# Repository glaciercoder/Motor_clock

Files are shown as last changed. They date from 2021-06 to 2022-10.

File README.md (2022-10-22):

# Motor_clock

## Day 1:

看到了链接觉得很好玩，想自己搞一个。

首先考虑到静音的需求，企图使用小步进，配合TMC202x控制芯片来用。

感谢 *小山嘉* 提供步进电机链接，使用拆机小型步进，成本很低。

发现问题在于TMC202x成本过高。

考虑到每个电机只需要两个状态，打算使用双稳态电磁阀 

发现一个视频：

[Mechnical Design](httNs://www.youtube.com/watch?v=ukRGbEUAVtM&feature=youtu.be)

打算搞这个曲线就可以用最多6个电机完成控制。

## Day 2:

和 *李金时* 一起研究机械结构，发现一些问题

1. 如果将连杆固结在数字轴中心，，数字翻动时会导致连杆的上下运动，所以使用凸轮结构。
2. 发现上述视频里的方形数字有点儿丑，想采用菱形和梯形数字，但是菱形和梯形数字在转动时出现干涉的现象，所以对干涉的问题进行研究。

### 参数初步规定：

连杆内拉3mm从隐藏变为显示，杆直径2mm，凸轮壁厚1mm

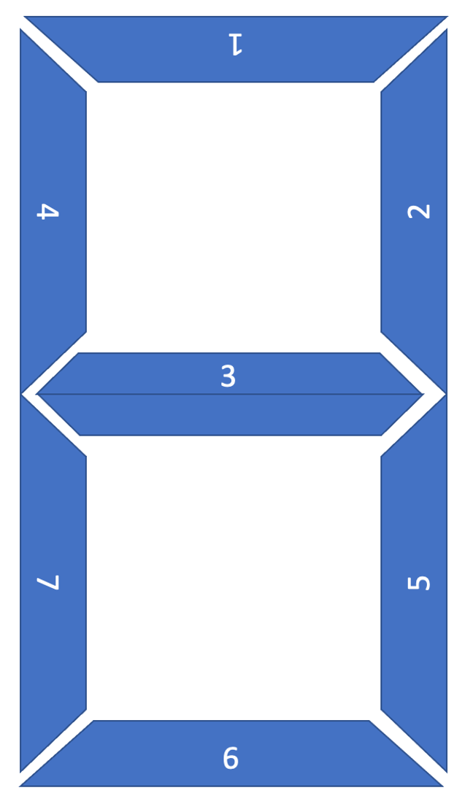
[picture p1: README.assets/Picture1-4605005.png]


### 凸轮设计：

记为放下状态(不显示)，为拉入状态（显示）

每$36^{\circ}$ 为一个变化时段，如果在该时段与下一时段交界处发生状态转变，则该时段最后$\Delta \theta$与下一时段$\Delta \theta$用于状态转变,对秒，$\Delta \theta = 10^{\circ}$;对分钟和小时,$\Delta \theta = 20^{\circ}$

| 编号/时序 |  1 | 2 | 3 | 4 | 5 | 6 | 7 | 8 | 9 | 0 |
| :---: | :--: | ---- | ---- | ---- | ---- | ---- | ---- | ---- | ---- | ---- |
| 1 |  N | P | P | N | P | P | P | P | P | P |
| 2 |  P | P | P | P | N | N | P | P | P | P |
| 3 |  N | P | P | P | P | P | N | P | P | N |
| 4 |  N | N | N | P | P | P | N | P | P | P |
| 5 |  P | N | P | P | P | P | P | P | P | P |
| 6 |  N | P | P | N | P | P | N | P | P | P |
| 7 |  N | P | N | N | N | P | N | P | N | P |

利用上述表格进行绘图，思考一番决定使用Matlab多项式拟合极坐标方程，$10^{\circ}$给一个点

发现完全没有必要，直接拿sw做，过渡处使用两段切线弧过渡

在一番苦战之后，终于把凸轮搞定了，下面将基于该尺寸完善连杆机构

## Day 3:

开始着手设计PCB，打算先拿一个板子，把配置都配好，在最终控制板上不再使用引脚配置TMC2208，

可以使用的其他电机驱动（A4998 TB6612FNG）

### PCB Design

考虑到电机供电问题，考虑使用电池供电,可通过外接电源切换

考虑到凸轮转动方向不变，可以将DIR全部共起来，同时考虑到秒针，分针时针凸轮转动频率相同，使用6个PWM引脚就可以，用PCA9685 I2C模拟PWM

时钟使用DS3231

## Day 4:

 意识到电机数量太多，功率较高，需要考虑怎么画转换电路，感谢 *高一川 梁迪轩* 的帮助

发现PCA9685 I2C模拟PWM的问题：输出PWM的频率都是相同的，这无法用于步进电机控制，所以用PCA来处理时钟和分钟8路PWM，秒针单独用两路PWM

## Day 5

发现DC5525可以通过机械结构直接断开内部电路，不同担心转换电路了,但是考虑到一个问题是，如果电源不是从DC005拔掉而是从插线板拔掉就出问题？

## Day 6

先把电机调通搞一套初步能用的代码，再继续画板子。

TMC2208可以使用USART模式（高级设置），也可以是向A4988那样使用简单的PWM输入，打算使用后者。但是电机第一次没有成功起转。后来发现应该将PDN引脚拉低，同时EN与单片机GND连接。

电机转动不太正常，主要的可能是该步进电机的额定电流未知，没有设置的比较好，打算买好一点的电机，再进行调试。

#### 学习用热风枪焊接IC

锡量极其重要，不要放太多，不然引脚大概率粘接

风速不能太低，不然多余焊锡熔而不走，也容易造成粘接

## Day 7

把电机调好了，真坑爹啊，以后一定要看清文档，M1A，M1B接的是一个绕组

Arduino delayMicrosecond 是微秒！

和李金时看了第一版结构，余量不足，无法装配

发现使用PCA9685的问题：如果使用PCA9685内部时钟，漂移可能会非常严重，如果使用外部时钟，配置困难且难以保证I2C正常工作，最终决定将电机驱动直接挂在GPIO上

在kicad里修改完footprint需要开一个新的lib保存，不然可能无法生效

开始layout了

## Day 8

layout好了，有几个问题需要思考：电机开环如何复位

准备使用红外对管进行复位

对于接地问题的讨论[接地](http://blog.sina.com.cn/s/blog_6471e1bb0100mrjp.html)

## Day 9

打样测试

## Day 10

考虑代码构建，使用状态机

[参考](https://learn.adafruit.com/multi-tasking-the-arduino-part-1)

每个loop先判断状态，用flag标记每个电机状态，然后用在mills执行相应动作

对于不同位置的电机设置不同的interval实现转动速度的控制

需要设计不同的细分

[millis rollover](https://arduino.stackexchange.com/questions/12587/how-can-i-handle-the-millis-rollover/12588#12588)

考虑一种处理溢出的方法：手写高精度,但实际上

[This is not a problem](https://www.gammon.com.au/millis)

## Day11

处理归零问题，机械归零不太好，设计了一种对管的方案：

使用一个狭缝，对对管的发射进行限制，然后在转盘上设计狭窄突出，与狭缝配合，提高精度，但是考虑到读取精度可能不高，而且加工精度也达不到很高，遂放弃该方案

采用磁编码器，使用AS5600，考虑到淘宝没有能够适用电机尺寸的PCB，打算自己设计

打算使用角块的方式进行盒子的装配，这样可以使装配变得简单

AS5600 不能设I2C地址，无语子

貌似AS5600L可以，但是也没说怎么设？ 无语子

*高一川* 给出针对I2C无法修改地址的应对策略，使用TCA9548A，非常有价值

## Day 12

第一次设计的PCB到了，有一个元件没有贴，极其难受，先尝试烧录程序，并调试DS3231

第一版板子的问题：

LED_Pin不在PWM引脚，修改DIR

没贴全

USB画反了，USB有没有画反取决于引脚顺序，而不是外形

软件部分，buffer难以清空，想写一个依靠串口进行初始化的程序。

## Day 13

画AS5600pcb

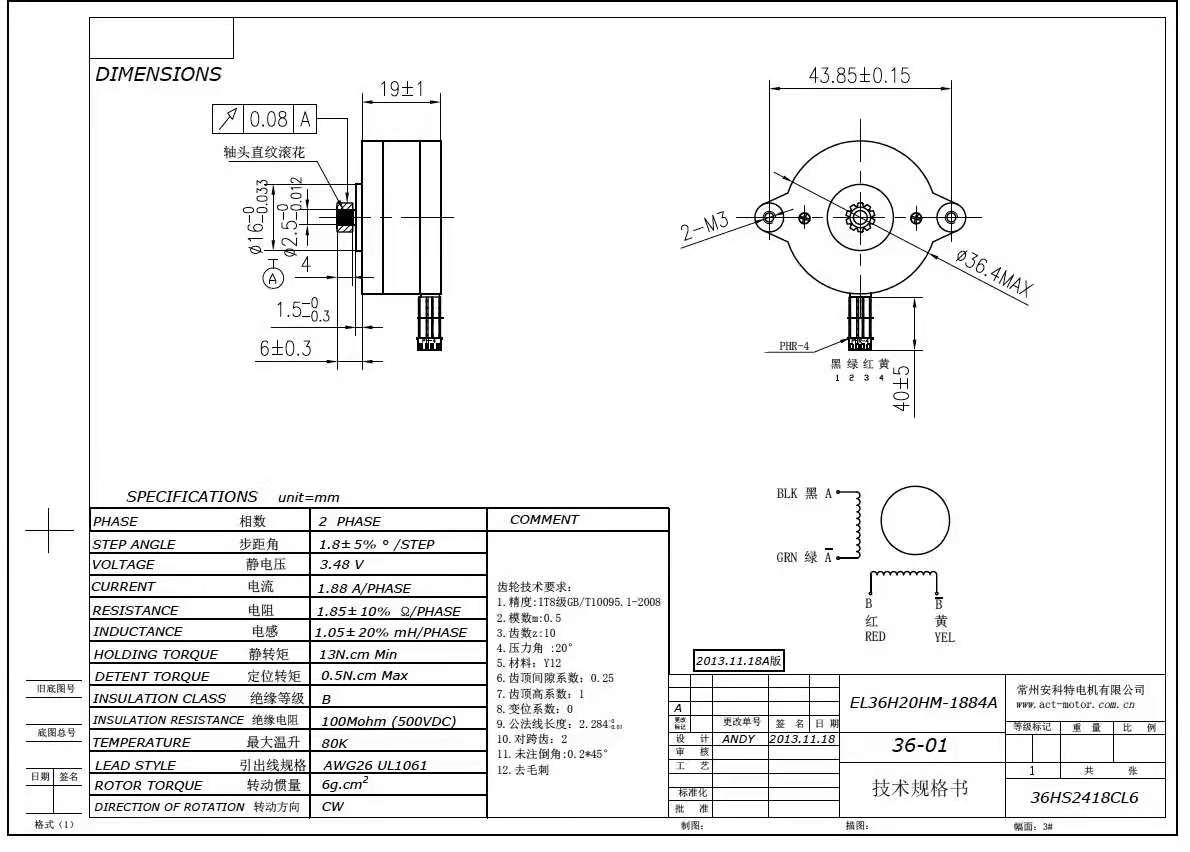
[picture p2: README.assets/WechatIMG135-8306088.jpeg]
WechatIMG135


修改第一版PCB，bug极多

1. ICSP接法：不是把一个的ICSP完全接到另一个的ICSP，targetRESET接法不一样！！！！！！需要接到10上
2. 不要在TX，RX上做LED，会让电压漂移
3. DTR必须接，不然不work，必须在DTR引脚到RESET之间串100nF电容，不然不work
4. CR3202 封装有问题

## Day14

调试第一版PCB，所用功能均正常

修改第一版PCB

1. 删去了DS3231的reset按钮，与MCU共RESET
2. PDN 直接接地
3. 加入了编码器接口
4. 加入蜂鸣器
5. 删去了无用的丝印
6. 修正了第一版的bug

机械装配遇到困难，采用数字板和连杆使用金属加工，其他部分3D打印的加工方式

## Day 15

讨论新的机械加工方案，打算使用齿轮传动，用固定座上的齿条驱动零件转动，但是加工仍然存在困难，考虑将元件放大两倍。

讨论盒子的设计方案

## Day 16

打印第二版零件，框加工有点儿贵，打算买现成的

南方小厂小批零件加工比北方大厂便宜很多，铝合金可直接激光切

## Day 17

调试第二版电路板，装配第二版机械零件。

第二版电路板控制部分工作正常，电源模块有问题，插上DC口出现烧坏的迹象，同时插入USB开始冒烟。4.7uH 电感挂了.

可能原因：电感许可电流太小，这是有可能的，在带LED之后确实需要比较大的电流输入，但是问题是没有接LED也挂了。 

六个电机接好，有一个不转，检查多次后无果，*夏博文* 提供帮助，发现是焊接connector时灌入过多的锡，导致connector在正面短路，焊接时一定要注意不能灌锡，应该尽量在一侧形成焊点。

六个编码器有一个不工作，怀疑是芯片的问题，打算重新做芯片

第三版软硬件修改：

1. 取消DS3231 RESET，实现一次上电一直记时的效果，对应的，把软件改成开机读取现在的时间，然后机械对钟。
2. 设置串口中断，只在接受到特定信号的时候进行DS3231设置
3. 将DIR换到非PWM引脚
4. 重画Buzzer电路，GPIO直接推不动

修改机械，使用内螺纹圆柱

内螺纹圆柱销 内径4x12x M3 100

M3x10 200个

## Day 18 19

重新修改机械结构，积累如下经验
==3D打印尽量设计螺丝固定等机构,尽可能少设计拼插==

==尽可能不要设计内槽道等结构，容易因为支撑等原因造成较大的误差==

==3D打印出的孔需要过一遍钻来保证精度==

==可以把层状3维结构拆分成2维，便于加工==

==sw建模使用树状装配体结构，将配合放在文件夹中便于修改，不要野配合==

==可以在适当的位置打孔，从而节省外包3D打印成本==

和李金时一起修3D打印机，

## Day 20
和nlc一起改了板子，主要是修改了电感的封装，新的板子功能正常。 <br/>
机械机构方面,nlc对齿条进行了两次修改，第一次延长了齿条长度，但是发现这个修改并不能解决啮合的问题，因此尝试将齿条整体抬高0.3mm，但是出现了上面的齿轮和齿条卡住的情况，对此，解决方案是把齿轮的高度下调一些。

## Day 21

- 发现一个大bug，凸轮结构控制滑块，考虑到每一层轨道控制的滑块要顺延90度，对应的轨道应该也转90度。

## Day 22

- nlc对底座进行了加强，避免了因底座在受力的情况下发生弯曲进而导致滑齿。

- ylw同学为了降低摩擦力非法使用了WD40，特此通报批评。

- wbc同学在调试过程中烧坏TMC2208一枚，工程经验又++。

## Day 23

- 302的门开了，nlc与wbc组装了一个完整的数字，调试顺利，而且噪声比预想的小很多。TMC2209驱动板的扭矩还是足够的。
  
  (https://youtube.com/shorts/_J2np6-Vw0g?feature=share)
  
 - 依然存在的问题&解决方案

    - 齿轮偶尔存在打滑的现象，原因可能是铜柱松动。由于无法精确设计铜柱的孔径大小，决定在竖直方向开孔，用M3螺丝锁住铜柱

## Day 24

- 新打印了座子与滑块，存在如下问题：

  - 由于3D打印机打印竖直方向的孔误差很大，M3螺丝容易打滑，考虑的解决方案是减小孔径。
  
  - 由于之前钢柱没完全固定，所以没有发现滑块和齿轮啮合过于紧的问题，打算先打印出来组装看看电机扭矩够不够。如果电机扭矩不够就降低滑块高度。

### 资料整理

[机械结构设计](httNs://www.youtube.com/watch?v=ukRGbEUAVtM&feature=youtu.be)

[TMC2208驱动](https://wiki.fysetc.com)

[TMC 接线](https://blog.csdn.net/weixin_42740222/article/details/88637535)

[Arduino TMC2208 lib](https://www.arduino.cc/reference/en/libraries/tmc2208stepper/)

[PCA9685电路设计](https://wenku.baidu.com/view/826d0d257c1cfad6185fa75c.html)

[PCA Arduino](https://learn.adafruit.com/16-channel-pwm-servo-driver/hooking-it-up)

[转换电路](https://www.eet-china.com/mp/a33537.html)

[DC5525](https://ask.zol.com.cn/x/5491238.html)

[Pin Mapping](https://www.arduino.cc/en/Hacking/PinMapping168)

[ATmega 328P-AU](https://forum.arduino.cc/t/atmega328-au/550838)

[Adafruit](https://learn.adafruit.com)

[AS5600](https://ams.com/as5600#tab/description)

[AS5600L](https://ams.com/documents/20143/36005/AS5600L_DS000545_3-00.pdf/7ade6878-7a32-2294-b88d-479d50fab6de)

[TCA9548](https://learn.adafruit.com/adafruit-tca9548a-1-to-8-i2c-multiplexer-breakout/downloads)

[I2C上拉电阻](https://www.zlg.cn/ipc/article/detail/id/690.html)

### 开销

中性笔(x)

买电机驱动模块 6个(x)

Niextube

嘉里创元件费（x）

云汉芯城元件费(x)

板子（x）

转接头（x）

DS3231模块(第一次)

DS3231模块(第二次) 

3D打印（200）

TCA9548A 模块

TPS561208DDCR

AS560 芯片(第一次)(x)

AS5600 芯片(第二次)

TCA9548A 芯片（30）

立创商城元件(x)

LED板（x）

第二次机械加工（860）

金属动板 (150)

嘉立创邮寄元件：TPS561208DDCR，TCA9548A(x), CH340G(x), 

WS2812(3m)(x)

邮寄处理费(x)

老铁：

中午吃饭. 51.5 (x)

《网络是怎样连接的》 91.64(x)

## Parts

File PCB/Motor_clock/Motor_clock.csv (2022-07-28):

ID | 指示符 | 软件包 | 数量 | 名称 | 供应商和参考
1 | VR1 | SOT95P280X110-6N | 1 | TPS561208DDCR
2 | BT1 | TE_796136-1 | 1 | BT_3v3
3 | C1 | C_0603_1608Metric | 1 | 100pF
4 | C2,C4 | C_0603_1608Metric | 2 | 1uF
5 | C3,C6,C13,C11 | C_0603_1608Metric | 4 | 22pF
6 | C5 | C_0805_2012Metric | 1 | 4.7uF
7 | C7 | C_0805_2012Metric | 1 | 22u
8 | C8 | C_0603_1608Metric | 1 | 0.1uF
9 | C9 | C_0805_2012Metric | 1 | 47uF
10 | D1 | LED_0603_1608Metric | 1 | LED
11 | J1 | JST_XH_S3B-XH-A-1_1x03_P2.50mm_Horizontal | 1 | WS2812
12 | J3 | JST_PH_S2B-PH-K_1x02_P2.00mm_Horizontal | 1 | Battery_input
13 | J4 | PinHeader_2x03_P2.54mm_Vertical | 1 | ICSP
14 | J5,J7 | JST_PH_B4B-PH-K_1x04_P2.00mm_Vertical | 2 | M_H_1
15 | J6 | JST_PH_B4B-PH-K_1x04_P2.00mm_Vertical | 1 | M_S_1
16 | J8 | JST_PH_B4B-PH-K_1x04_P2.00mm_Vertical | 1 | M_S_2
17 | J9 | JST_PH_B4B-PH-K_1x04_P2.00mm_Vertical | 1 | M_M_1
18 | J10 | JST_PH_B4B-PH-K_1x04_P2.00mm_Vertical | 1 | M_M_2
19 | L1 | L_7.3x7.3_H4.5 | 1 | 4.7uH
20 | R1,R3,R4,R8,R9 | R_0603_1608Metric | 5 | 1k
21 | R2,R5 | R_0603_1608Metric | 2 | 4k7
22 | R7 | R_0603_1608Metric | 1 | 10k
23 | SW2 | SW_Push_1P1T_NO_6x6mm_H9.5mm | 1 | SW_Push
24 | U2 | TQFP-32_7x7mm_P0.8mm | 1 | ATmega328P-AU
25 | Y1 | Crystal_SMD_3225-4Pin_3.2x2.5mm | 1 | 16Mhz
26 | U3 | TMC2208 | 1 | M_H_1
27 | U4 | TMC2208 | 1 | M_S_1
28 | U5 | TMC2208 | 1 | M_H_2
29 | U6 | TMC2208 | 1 | M_S_2
30 | U7 | TMC2208 | 1 | M_M_1
31 | U8 | TMC2208 | 1 | M_M_2
32 | J2 | NINIGI_DC-005 | 1 | Barrel_Jack_Switch
33 | H2,H4,H3,H1 | MountingHole_3.2mm_M3 | 4 | MountingHole
34 | J12 | JST_PH_B4B-PH-K_1x04_P2.00mm_Vertical | 1 | Enc_M_2
35 | J13 | JST_PH_B4B-PH-K_1x04_P2.00mm_Vertical | 1 | Enc_H_2
36 | J14 | JST_PH_B4B-PH-K_1x04_P2.00mm_Vertical | 1 | Enc_S_2
37 | J15 | JST_PH_B4B-PH-K_1x04_P2.00mm_Vertical | 1 | Enc_S_1
38 | J16 | JST_PH_B4B-PH-K_1x04_P2.00mm_Vertical | 1 | Enc_M1
39 | J17 | JST_PH_B4B-PH-K_1x04_P2.00mm_Vertical | 1 | Enc_H_1
40 | U10 | TSSOP-24_4.4x7.8mm_P0.65mm | 1 | TCA9548APWR
41 | U1 | SOIC-16W_7.5x10.3mm_P1.27mm | 1 | DS3231M
42 | C10 | C_0603_1608Metric | 1 | 10uF
43 | C12,C14,C15 | C_0603_1608Metric | 3 | 100nF
44 | D2,D3 | D_SMA | 2 | 1N5819
45 | Y2 | Crystal_SMD_3225-4Pin_3.2x2.5mm | 1 | 12Mhz
46 | U9 | SOIC-16_3.9x9.9mm_P1.27mm | 1 | CH340G
47 | J11 | MicroXNJ | 1 | USB_B_Micro
48 | BZ1 | buzzer | 1 | Buzzer
49 | Q1 | SOT-23 | 1 | Q_NPN_BEC
50 | R6 | R_1206_3216Metric | 1 | 56.2k
51 | G*** | logo | 1 | LOGO

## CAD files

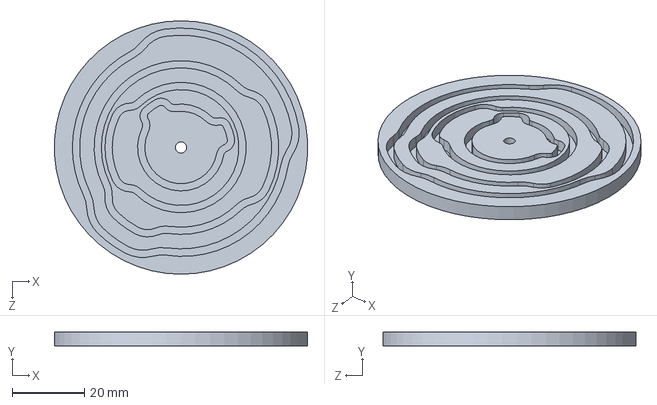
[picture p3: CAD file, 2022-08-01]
code/clock/clock_base.SLDPRT
69.9 x 4.00 x 70.0 mm

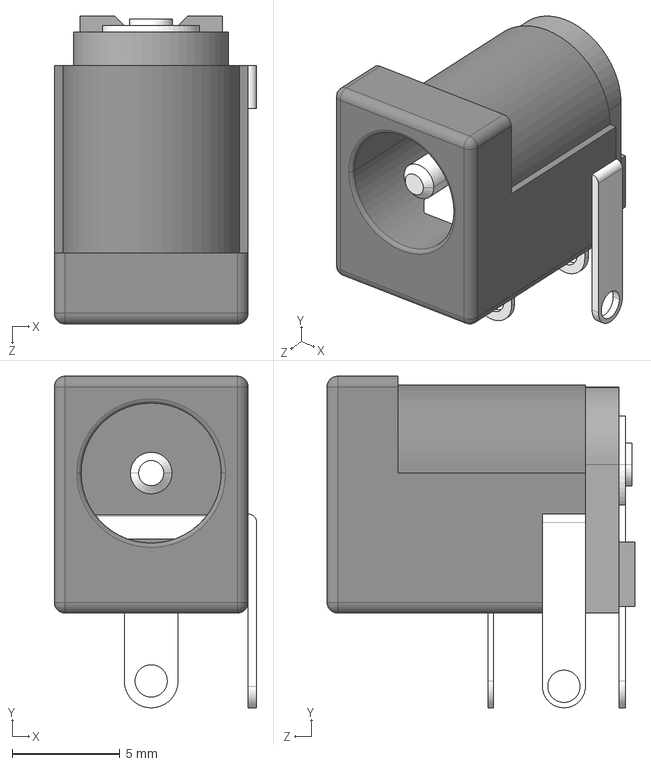
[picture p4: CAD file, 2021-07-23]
PCB/Motor_clock/DC-005/DC-005.step
9.40 x 15.4 x 14.3 mm

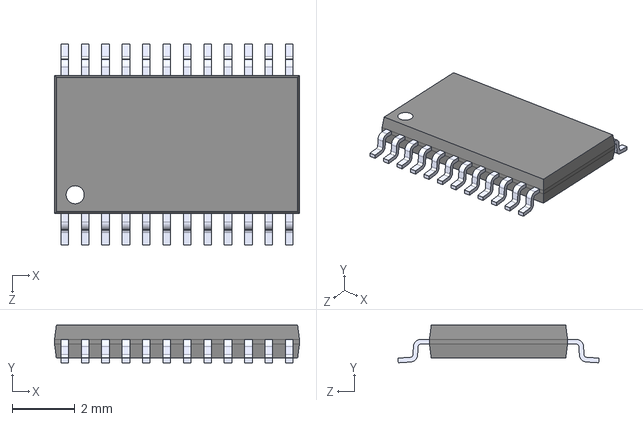
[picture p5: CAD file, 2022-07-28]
PCB/Motor_clock/TCA9548APWR/TCA9548APWR.step
7.80 x 1.20 x 6.40 mm

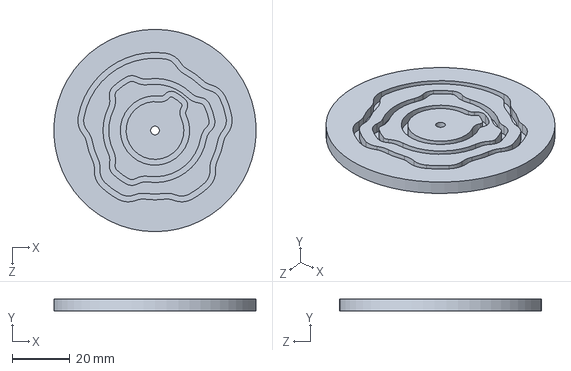
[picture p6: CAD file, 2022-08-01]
code/clock/clock_base_2.SLDPRT
69.9 x 4.00 x 70.0 mm

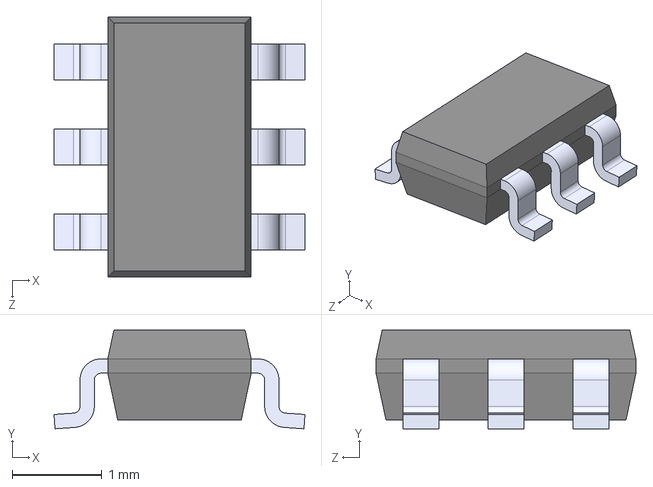
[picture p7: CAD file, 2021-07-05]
PCB/Motor_clock/TPS561208DDCR/TPS561208DDCR.step
2.80 x 1.10 x 2.90 mm

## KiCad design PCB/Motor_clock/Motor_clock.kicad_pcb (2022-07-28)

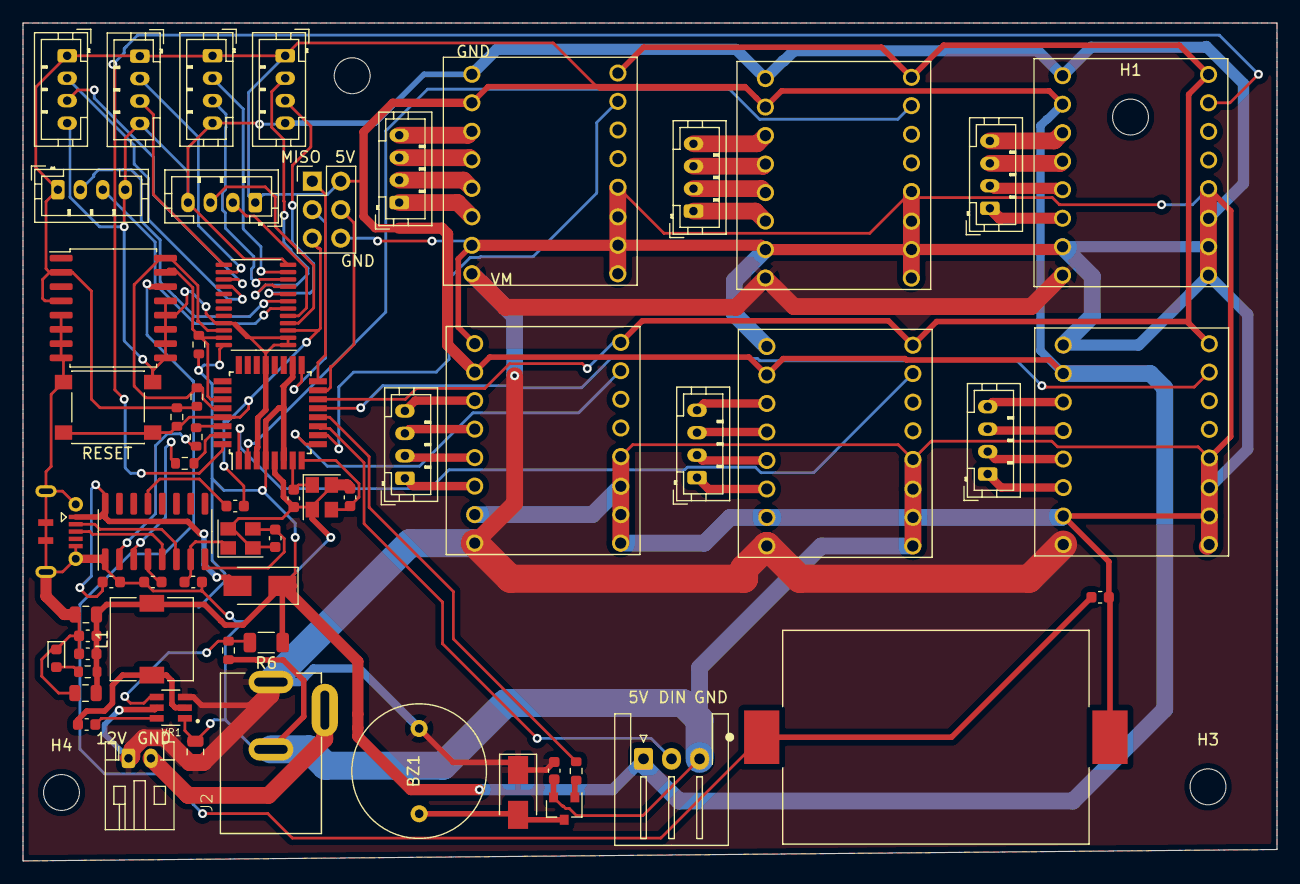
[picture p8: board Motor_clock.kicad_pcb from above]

Board: 2 copper layers, 111.8 x 74.7 mm, 66 parts (0 on the bottom side), 75 nets.

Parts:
BT1: BT_3v3; TE_796136-1
BZ1: Buzzer; buzzer
C1: 100pF; C_0603_1608Metric
C2, C4: 1uF; C_0603_1608Metric
C3, C6, C11, C13: 22pF; C_0603_1608Metric
C5: 4.7uF; C_0805_2012Metric
C7: 22u; C_0805_2012Metric
C8: 0.1uF; C_0603_1608Metric
C9: 47uF; C_0805_2012Metric
C10: 10uF; C_0603_1608Metric
C12, C14, C15: 100nF; C_0603_1608Metric
D1: LED; LED_0603_1608Metric
D2, D3: 1N5819; D_SMA
H1, H2, H3, H4: MountingHole; MountingHole_3.2mm_M3
J1: WS2812; JST_XH_S3B-XH-A-1_1x03_P2.50mm_Horizontal
J2: Barrel_Jack_Switch; NINIGI_DC-005
J3: Battery_input; JST_PH_S2B-PH-K_1x02_P2.00mm_Horizontal
J4: ICSP; PinHeader_2x03_P2.54mm_Vertical
J5, J7: M_H_1; JST_PH_B4B-PH-K_1x04_P2.00mm_Vertical
J6: M_S_1; JST_PH_B4B-PH-K_1x04_P2.00mm_Vertical
J8: M_S_2; JST_PH_B4B-PH-K_1x04_P2.00mm_Vertical
J9: M_M_1; JST_PH_B4B-PH-K_1x04_P2.00mm_Vertical
J10: M_M_2; JST_PH_B4B-PH-K_1x04_P2.00mm_Vertical
J11: USB_B_Micro; MicroXNJ
J12: Enc_M_2; JST_PH_B4B-PH-K_1x04_P2.00mm_Vertical
J13: Enc_H_2; JST_PH_B4B-PH-K_1x04_P2.00mm_Vertical
J14: Enc_S_2; JST_PH_B4B-PH-K_1x04_P2.00mm_Vertical
J15: Enc_S_1; JST_PH_B4B-PH-K_1x04_P2.00mm_Vertical
J16: Enc_M1; JST_PH_B4B-PH-K_1x04_P2.00mm_Vertical
J17: Enc_H_1; JST_PH_B4B-PH-K_1x04_P2.00mm_Vertical
L1: 4.7uH; L_7.3x7.3_H4.5
Q1: Q_NPN_BEC; SOT-23
R1, R3, R4, R8, R9: 1k; R_0603_1608Metric
R2, R5: 4k7; R_0603_1608Metric
R6: 56.2k; R_1206_3216Metric
R7: 10k; R_0603_1608Metric
SW2: SW_Push; SW_Push_1P1T_NO_6x6mm_H9.5mm
U1: DS3231M; SOIC-16W_7.5x10.3mm_P1.27mm
U2: ATmega328P-AU; TQFP-32_7x7mm_P0.8mm
U3: M_H_1; TMC2208
U4: M_S_1; TMC2208
U5: M_H_2; TMC2208
U6: M_S_2; TMC2208
U7: M_M_1; TMC2208
U8: M_M_2; TMC2208
U9: CH340G; SOIC-16_3.9x9.9mm_P1.27mm
U10: TCA9548APWR; TSSOP-24_4.4x7.8mm_P0.65mm
VR1: TPS561208DDCR; SOT95P280X110-6N
Y1: 16Mhz; Crystal_SMD_3225-4Pin_3.2x2.5mm
Y2: 12Mhz; Crystal_SMD_3225-4Pin_3.2x2.5mm

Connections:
12V: BZ1.1 (-), C7.1, C15.1, D3.1 (K), J2.1, J3.1, U3.9 (VM), U4.9 (VM), U5.9 (VM), U6.9 (VM), U7.9 (VM), U8.9 (VM), VR1.3 (VIN), VR1.5 (EN)
+5V: C2.1, C4.1, C5.1, C9.1, D2.1 (K), J1.1, J4.2, J12.1, J13.1, J14.1, J15.1, J16.1, J17.1, L1.2, R1.1, R2.1, R5.1, R6.1, R8.1, U1.2 (VCC), U1.4 (~RST), U2.4 (VCC), U2.6 (VCC), U2.18 (AVCC), U3.15 (VIO), U4.15 (VIO), U5.15 (VIO), U6.15 (VIO), U7.15 (VIO), U8.15 (VIO), U10.24 (VCC)
BAT_GND: J2.2, J3.2
Buzzer: R9.2, U2.12 (PB0)
D+: J11.3 (D+), U9.5 (UD+)
D-: J11.2 (D-), U9.6 (UD-)
DIR: U2.14 (PB2), U3.8 (DIR), U4.8 (DIR), U5.8 (DIR), U6.8 (DIR), U7.8 (DIR), U8.8 (DIR)
LED_DA: J1.2, U2.11 (PD7)
MISO: J4.1, U2.16 (PB4)
MOSI: J4.4, U2.15 (PB3)
unnamed: BT1.1 (+), C1.1, U1.14 (VBAT)
unnamed: BZ1.2 (+), D3.2 (A), Q1.3 (C)
unnamed: C8.2, L1.1, VR1.2 (SW)
unnamed: C11.1, U9.7 (XI), Y2.1
unnamed: C12.1, U9.4 (V3)
unnamed: C13.1, U9.8 (XO), Y2.3
unnamed: C14.1, U9.13 (~DTR)
unnamed: D1.2 (A), R8.2
unnamed: J5.1, U3.11 (M1B)
unnamed: J5.2, U3.12 (M1A)
unnamed: J5.3, U3.13 (M2A)
unnamed: J5.4, U3.14 (M2B)
unnamed: J6.1, U4.11 (M1B)
unnamed: J6.2, U4.12 (M1A)
unnamed: J6.3, U4.13 (M2A)
unnamed: J6.4, U4.14 (M2B)
unnamed: J7.1, U5.11 (M1B)
unnamed: J7.2, U5.12 (M1A)
unnamed: J7.3, U5.13 (M2A)
unnamed: J7.4, U5.14 (M2B)
unnamed: J8.1, U6.11 (M1B)
unnamed: J8.2, U6.12 (M1A)
unnamed: J8.3, U6.13 (M2A)
unnamed: J8.4, U6.14 (M2B)
unnamed: J9.1, U7.11 (M1B)
unnamed: J9.2, U7.12 (M1A)
unnamed: J9.3, U7.13 (M2A)
unnamed: J9.4, U7.14 (M2B)
unnamed: J10.1, U8.11 (M1B)
unnamed: J10.2, U8.12 (M1A)
unnamed: J10.3, U8.13 (M2A)
unnamed: J10.4, U8.14 (M2B)
unnamed: Q1.1 (B), R9.1
unnamed: R3.2, U2.30 (PD0)
unnamed: R4.2, U2.31 (PD1)
P0: U2.13 (PB1), U3.7 (STEP)
P1: U2.32 (PD2), U5.7 (STEP)
P2: U2.1 (PD3), U7.7 (STEP)
P3: U2.2 (PD4), U8.7 (STEP)
P4: U2.9 (PD5), U4.7 (STEP)
P5: U2.10 (PD6), U6.7 (STEP)
PDN: BT1.2 (-), C1.2, C2.2, C3.1, C4.2, C5.2, C6.2, C7.2, C9.2, C10.2, C11.2, C12.2, C13.2, C15.2, D1.1 (K), J1.3, J2.3, J4.6, J11.5 (GND), J11.6 (Shield), J12.4, J13.4, J14.4, J15.4, J16.4, J17.4, Q1.2 (E), R7.2, SW2.1, U1.5 (GND), U1.6 (GND), U1.7 (GND), U1.8 (GND), U1.9 (GND), U1.10 (GND), U1.11 (GND), U1.12 (GND), U1.13 (GND), U2.3 (GND), U2.5 (GND), U2.21 (GND), U3.1 (EN), U3.2 (MS1), U3.3 (MS2), U3.4 (PDN), U3.10 (GND), U3.16 (GND), U4.1 (EN), U4.2 (MS1), U4.3 (MS2), U4.4 (PDN), U4.10 (GND), U4.16 (GND), U5.1 (EN), U5.2 (MS1), U5.3 (MS2), U5.4 (PDN), U5.10 (GND), U5.16 (GND), U6.1 (EN), U6.2 (MS1), U6.3 (MS2), U6.4 (PDN), U6.10 (GND), U6.16 (GND), U7.1 (EN), U7.2 (MS1), U7.3 (MS2), U7.4 (PDN), U7.10 (GND), U7.16 (GND), U8.1 (EN), U8.2 (MS1), U8.3 (MS2), U8.4 (PDN), U8.10 (GND), U8.16 (GND), U9.1 (GND), U10.1 (A0), U10.2 (A1), U10.12 (GND), U10.21 (A2), VR1.1 (GND), Y1.2, Y1.4, Y2.2, Y2.4
RESET: C14.2, J4.5, R1.2, SW2.2, U2.29 (~RESET/PC6), U10.3 (~RESET)
RX: R4.1, U9.3 (RXD)
SC0: J14.2, U10.5 (SC0)
SC1: J15.2, U10.7 (SC1)
SC2: J12.2, U10.9 (SC2)
SC3: J16.2, U10.11 (SC3)
SC4: J13.2, U10.14 (SC4)
SC5: J17.2, U10.16 (SC5)
SCK: J4.3, U2.17 (PB5)
SCL: R5.2, U1.16 (SCL), U2.28 (PC5), U10.22 (SCL)
SD0: J14.3, U10.4 (SD0)
SD1: J15.3, U10.6 (SD1)
SD2: J12.3, U10.8 (SD2)
SD3: J16.3, U10.10 (SD3)
SD4: J13.3, U10.13 (SD4)
SD5: J17.3, U10.15 (SD5)
SDA: R2.2, U1.15 (SDA), U2.27 (PC4), U10.23 (SDA)
TX: R3.1, U9.2 (TXD)
VBST: C8.1, VR1.6 (VBST)
VFB: R6.2, R7.1, VR1.4 (VFB)
VIN: C10.1, D2.2 (A), J11.1 (VBUS), U9.16 (VCC)
XTAL1: C3.2, U2.7 (XTAL1/PB6), Y1.1
XTAL2: C6.1, U2.8 (XTAL2/PB7), Y1.3

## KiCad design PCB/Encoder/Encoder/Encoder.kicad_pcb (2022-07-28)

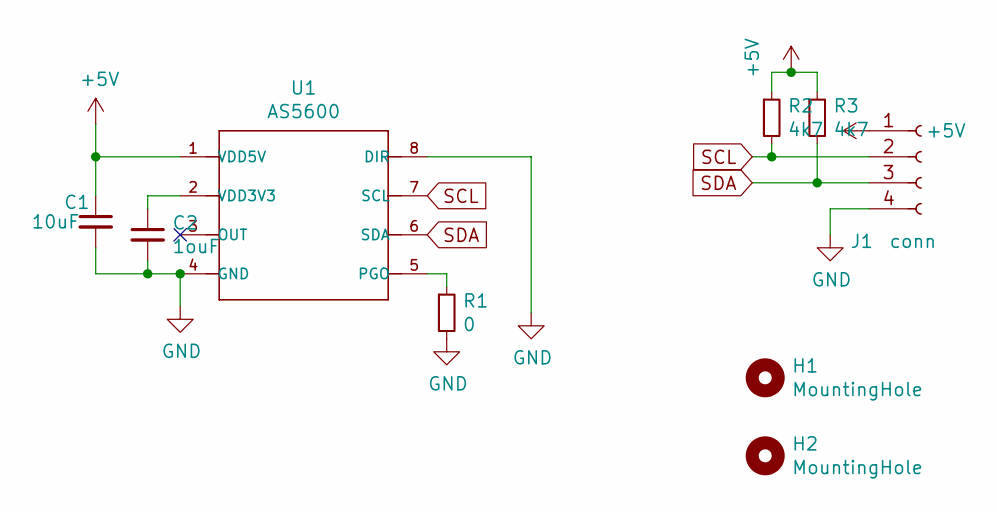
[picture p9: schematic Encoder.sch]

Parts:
C1: 10uF; C_0805_2012Metric
C2: 1ouF; C_0805_2012Metric
H1, H2: MountingHole; MountingHole_3.2mm_M3
J1: conn; JST_PH_B4B-PH-K_1x04_P2.00mm_Vertical
R1: 0; R_1206_3216Metric
R2, R3: 4k7; R_0603_1608Metric
U1: AS5600

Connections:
+5V: C1.1, J1.1, R2.1, R3.1, U1.1 (VDD5V)
GND: C1.2, C2.2, J1.4, R1.2, U1.4 (GND), U1.8 (DIR)
unnamed: C2.1, U1.2 (VDD3V3)
unnamed: R1.1, U1.5 (PGO)
SCL: J1.2, R2.2, U1.7 (SCL)
SDA: J1.3, R3.2, U1.6 (SDA)

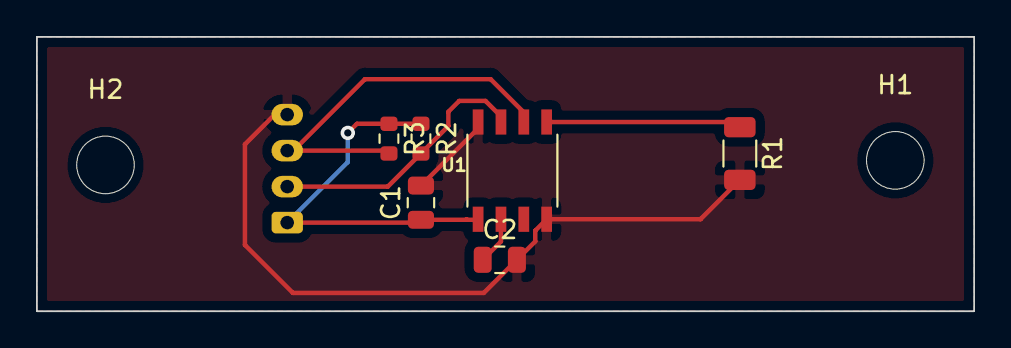
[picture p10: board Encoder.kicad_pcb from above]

Board: 2 copper layers, 52.1 x 15.2 mm, 9 parts (1 on the bottom side), 6 nets.

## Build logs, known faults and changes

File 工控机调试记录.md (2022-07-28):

# CNC调试记录

从AIR获得工控机

必须使用并口通信，由于主机并没有并口，使用PCI转并口

驱动一开始打算在官网下载，但是官网驱动不能在英文环境下安装，遂直接使用网络在设备管理器中更新驱动，实现目标。

一开始使用windows 7 64bit，无法工作，于是使用32bit系统

换成32bit系统自后，按照说明破解之后，启动后黑屏

Mach3 破解版总是出现问题，最终打算使用Linux CNC

Linux CNC坑也多，学习学习视频准备实操，把xml导入Mach读出配置，按此配置设置，不work

最后换用旧CNC主板，work，但是Home不对

AXIS is the default GUI

最新：

配置里的BothLimits and HOME 是指home switch，问题是：我们的机子上是否有home switch

一个limit switch可以被用作home switch

MDI stands for manual data input

Modes of operation:

Homing can only be excuted in manual mode

Run a full gcode can only be done in auto mode

G53：机械坐标，在homing后把Home的点设置成原点

FeedoverRide 类似于速度超调

搞清楚 **Coordinate Display**

和 Manual Control

目前还有不太理解的问题就是坐标的问题和换刀具的问题

### Gcode

Gcode 的structure:

Program -> lines -> word

Words

G90 : 绝对坐标

```gcode
G90
G0 X2.5(rapid move to coordinate X2.5 including any offsets in effect)
```

G91: 相对坐标

```gcode
G91 (set incremental distance mode)
G0 X2.5 (rapid move 2.5 from current position along the X axis)
```

M2 M30 :终止程序

G1 : Linear Motion

```gcode
G90 (set absolute distance mode)
G1 X1.2 Y-3 F10 (linear move at a feed rate of 10 from current position to X1.2 Y-3)
Z-2.3 (linear move at same feed rate from current position to Z-2.3)
Z1 F25 (linear move at a feed rate of 25 from current position to Z1)
M2 (end program)
```

- N040 G53 X0 Y0 Z0 回到原点

[Homing](http://linuxcnc.org/docs/2.4/html/config_ini_homing.html)

在home的速度上有个tradeoff，如果过于快，可能会撞到限位上，如果过于慢，会等待很长时间

## Home

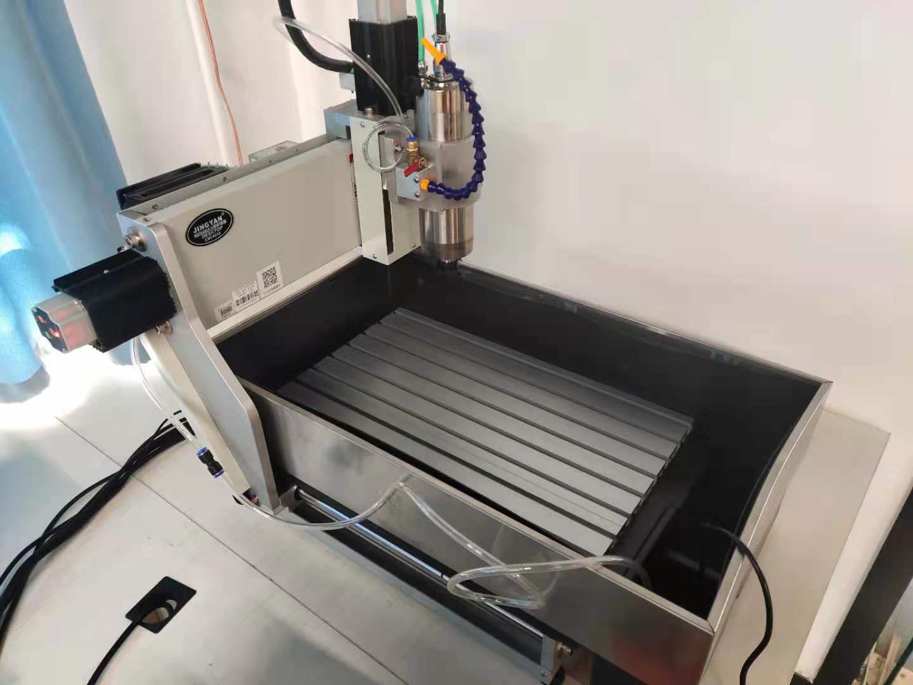
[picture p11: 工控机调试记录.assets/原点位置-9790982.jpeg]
原点位置


如上图，这是一开始机器的home的位置，每次home后机器会回到这一点，然后将此点处坐标标记成（0，0，0），然后在接下来的运动中，机器只能在0 - Max范围内移动，然而bug在于，三轴继续正向移动只会触发限位开关，所以三轴实际上无法进一步移动，这个bug让我反思stepconf中每个轴配置中的Home location, table travel, home switch location 这几个量

首先更改home location 在更改之后，仍然运动到限位开关处，但是此点处坐标不再是(0,0,0)而是home location的值，而机器的行程仍然是0-Max，这使得三轴不再是被卡到home处，通过这个也知道了table travel中的值正是基于G53坐标的

思考CNC总是回到A点而不是B点的原因，想到一种可能的原因：我们没有home switch，所以机器只能朝一个方向试探，在试探过程汇总trip到了limit switch，于是在A点停止，能否通过更改试探的方向，使得机器能在B点home呢？因为我想使用正的坐标，这样可以对后续的G code采用的坐标系统进行一个sanity check 

在stepconf 中修改了home search Velocity ，将其调成负值

它    W   O.   R.     K 了！

由于我们使用的4060CNC在触发Limit switch 的时候会自动向后移动一个固定offset，所以不必担心serach velocity带来的问题，可以把它调大一点儿

### Gcode converter

https://listoffreeware.com/free-dxf-to-gcode-converter-software-windows/

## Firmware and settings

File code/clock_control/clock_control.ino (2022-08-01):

#define FASTLED_INTERNAL
#define NUM_LEDS 3
#define LED_TYPE WS2812
#define COLOR_ORDER GRB
#define TCAADDR 0x70
#define ENCADDR 0x36
#include <Wire.h>
#include<DS3231.h>
#include <TimerOne.h>
#include <AS5600.h>
#include <FastLED.h>
DS3231 clock_for_motor;
CRGB leds[NUM_LEDS];

//Pin def
const int step_H_1 = 9;
const int step_H_2 = 2;
const int step_M_1 = 3;
const int step_M_2 = 4;
const int step_S_1 = 5;
const int step_S_2 = 6;
const int dirPin = 10;
const int LED_DATA = 7;
const int Buzzer = 8;
AS5600 encoder[6];

//state machine
bool State_H_1 = 0;
bool State_H_2 = 0;
bool State_M_1 = 0;
bool State_M_2 = 0;
bool State_S_1 = 0;
bool State_S_2 = 0;
bool ENA_H_1 = 0;
bool ENA_H_2 = 0;
bool ENA_M_1 = 0;
bool ENA_M_2 = 0;
bool ENA_S_1 = 0;
//Intervals
//1.8 degrees per step (ms = 1/8)
//1s 20 x 8 steps
//1 step for 6250us
const unsigned long interval_s = 250;//
const unsigned long interval_m = 2 * interval_s;
const unsigned long interval_h = 5 * interval_s;
unsigned long  micros_s = 0;
unsigned long  micros_m_2 = 0;
unsigned long  micros_m_1 = 0;
unsigned long  micros_h_2 = 0;
unsigned long  micros_h_1 = 0;


//timer vars
int time_for_motor[3];
int angle[6];//angle 0-5 for s2,21,m2,m1,h2,n1 respectively
bool h12 = false;
bool apm;


void setup() {
  pinMode(step_H_1, OUTPUT);
  pinMode(step_H_2, OUTPUT);
  pinMode(step_M_1, OUTPUT);
  pinMode(step_M_2, OUTPUT);
  pinMode(step_S_1, OUTPUT);
  pinMode(step_S_2, OUTPUT);
  pinMode(dirPin, OUTPUT);
  digitalWrite(dirPin, LOW);
  Wire.begin();
  Serial.begin(115200);
  LEDS.addLeds<LED_TYPE, LED_DATA, COLOR_ORDER>(leds, NUM_LEDS);
  FastLED.setBrightness(255);
  Encoder_init();
  
  while (Serial.available() > 0) {
    Serial.flush();
  }
  Time_Init(time_for_motor);
  Timer1.initialize(interval_s); //Initialize timer with 1 second period
  Timer1.attachInterrupt(PWM_s);  
}

void loop() {
  ENA_S_1 = ENA_H_1 =  ENA_H_2 = ENA_M_1 = ENA_M_2 = 0;
  CheckState(ENA_H_1, ENA_H_2, ENA_M_1, ENA_M_2, ENA_S_1, time_for_motor);
  if (ENA_S_1)
    if (micros() - micros_s > interval_s) {
      State_S_1 = !State_S_1;
      digitalWrite(step_S_1, State_S_2 ? HIGH : LOW);
      micros_s = micros();
    }

  if (ENA_M_2)
    if (micros() - micros_m_2 > interval_m) {
      State_M_2 = !State_M_2;
      digitalWrite(step_M_2, State_M_2 ? HIGH : LOW);
      micros_m_2 = micros();
    }

  if (ENA_M_1)
    if (micros() - micros_m_1 > interval_m) {
      State_M_1 = !State_M_1;
      digitalWrite(step_M_1, State_M_2 ? HIGH : LOW);
      micros_m_1 = micros();
    }

  if (ENA_H_2)
    if (micros() - micros_h_2 > interval_h) {
      State_H_2 = !State_H_2;
      digitalWrite(step_H_2, State_H_2 ? HIGH : LOW); 
      micros_h_2 = micros();
    }

  if (ENA_H_1)
    if (micros() - micros_h_1 > interval_h) {
      State_H_1 = !State_H_1;
      digitalWrite(step_H_1, State_H_1 ? HIGH : LOW);
      micros_h_1 = micros();
    }


  time_for_motor[0] = clock_for_motor.getHour(h12, apm);
  time_for_motor[1] = clock_for_motor.getMinute();
  time_for_motor[2] = clock_for_motor.getSecond();
  Readangle(angle);
  printTime(time_for_motor);
}


void clock_for_motorRun(void){
  if (ENA_S_1)
    if (micros() - micros_s > interval_s) {
      State_S_1 = !State_S_1;
      digitalWrite(step_S_1, State_S_2 ? HIGH : LOW);
      micros_s = micros();
    }

  if (ENA_M_2)
    if (micros() - micros_m_2 > interval_m) {
      State_M_2 = !State_M_2;
      digitalWrite(step_M_2, State_M_2 ? HIGH : LOW);
      micros_m_2 = micros();
    }

  if (ENA_M_1)
    if (micros() - micros_m_1 > interval_m) {
      State_M_1 = !State_M_1;
      digitalWrite(step_M_1, State_M_2 ? HIGH : LOW);
      micros_m_1 = micros();
    }

  if (ENA_H_2)
    if (micros() - micros_h_2 > interval_h) {
      State_H_2 = !State_H_2;
      digitalWrite(step_H_2, State_H_2 ? HIGH : LOW); 
      micros_h_2 = micros();
    }

  if (ENA_H_1)
    if (micros() - micros_h_1 > interval_h) {
      State_H_1 = !State_H_1;
      digitalWrite(step_H_1, State_H_1 ? HIGH : LOW);
      micros_h_1 = micros();
    }
}

void PWM_s(void) {
  State_S_2 = !State_S_2;
  digitalWrite(step_S_2, State_S_2 ? HIGH : LOW);
  digitalWrite(Buzzer, State_S_2 ? HIGH : LOW);
}

void tcaselect(uint8_t i){
  if(i > 7) return;
  Wire.beginTransmission(TCAADDR);
  Wire.write(1 << i);
  Wire.endTransmission();
}

void Readangle(int angle[]){
  for(int i = 0;i < 6;i++){
    tcaselect(i);
    Wire.beginTransmission(ENCADDR);
    if (!Wire.endTransmission()){
      angle[i] = encoder[i].readAngle();
          //Serial.print("Angle "); Serial.print(i);Serial.print(" = ");Serial.println(angle[i]);
    }
  }               
}

void convert_angle(int startangle[],int time_for_motor[]){
  startangle[0] = time_for_motor[0] / 10 * 36;
  startangle[1] = time_for_motor[0] % 10 * 36;
  startangle[2] = time_for_motor[1] / 10 * 36;
  startangle[3] = time_for_motor[1] % 10 * 36;
  startangle[4] = time_for_motor[2] / 10 * 36;
  startangle[5] = time_for_motor[2] % 10 * 36;  
}

bool CompareAngle(int startangle[], int angle[]){
  bool equal = true;
  for(int i = 0;i < 6;i++){
    equal  = equal && ((abs(startangle[i] - angle[i])) < 1);
  }
  return equal;
}

void Time_Init(int time_for_motor[])
{
  byte index = 0;
  char endMarker = '\n';
  char rc;
  char Serial_Res[6];
  Serial.print("Set the time:\n");

  while (true) {
    while (Serial.available() == 0);
    rc = Serial.read();
    if (rc != endMarker)
      Serial_Res[index++] = rc;
    else
      break;
  }

  time_for_motor[0] = (Serial_Res[0] - '0') * 10 + (Serial_Res[1] - '0');
  time_for_motor[1] = (Serial_Res[2] - '0') * 10 + (Serial_Res[3] - '0');
  time_for_motor[2] = (Serial_Res[4] - '0') * 10 + (Serial_Res[5] - '0');
  clock_for_motor.setSecond(time_for_motor[2]);//Set the second
  clock_for_motor.setMinute(time_for_motor[1]);//Set the minute
  clock_for_motor.setHour(time_for_motor[0]);  //Set the hour
  Serial.print("Time Set::");
  printTime(time_for_motor);

  micros_s = micros();
  micros_m_2 = micros();
  micros_m_1 = micros();
  micros_h_2 = micros();
  micros_h_1 = micros();
  //Checkclock_for_motor(time);
}



//closed loop control
void Checkclock_for_motor(int time_for_motor[]){
  int startangle[6];
  convert_angle(startangle, time_for_motor);
  Readangle(angle);
  ENA_H_1 = ENA_H_2 = ENA_M_1 = ENA_M_2 = ENA_S_1 = 1;
  Timer1.attachInterrupt(PWM_s);
  while(! CompareAngle(startangle, angle)){
     if((abs(startangle[0] - angle[0])) < 1) ENA_H_1 = 0;
     if((abs(startangle[1] - angle[1])) < 1) ENA_H_2 = 0;
     if((abs(startangle[2] - angle[2])) < 1) ENA_M_1 = 0;
     if((abs(startangle[3] - angle[3])) < 1) ENA_M_2 = 0;
     if((abs(startangle[4] - angle[4])) < 1) ENA_S_1 = 0;
     if((abs(startangle[5] - angle[5])) < 1) Timer1.detachInterrupt();
     clock_for_motorRun();
  }
}
void CheckState(bool& ENAH1, bool& ENAH2, bool& ENAM1, bool& ENAM2, bool& ENAS1, int time_for_motor[])
{
  ENAS1 = (time_for_motor[2] % 10 == 9) ? true : false;
  ENAM2 = (time_for_motor[2] >= 58) ? true : false;
  ENAM1 = ((time_for_motor[1] % 10 == 9) && (time_for_motor[2] >= 58)) ? true : false;
  ENAH2 = ((time_for_motor[1] == 59) && (time_for_motor[2] >= 55) ) ? true : false;
  ENAH1 = ((time_for_motor[0] % 10 == 9) && (time_for_motor[2] >= 55)) ? true : false;
}


void Encoder_init(){
  for (uint8_t t=0; t<6; t++) {
      tcaselect(t);
      Serial.print("TCA Port #"); Serial.println(t);
      Wire.beginTransmission(ENCADDR);
      if (!Wire.endTransmission()) {
          Serial.print("Found Encoder "); Serial.println(t);
      }
  }  
  Serial.println("\ndone");
}


float convertRawAngleToDegrees(word newAngle)
{
  /* Raw data reports 0 - 4095 segments, which is 0.087 of a degree */
  float retVal = newAngle * 0.087;
  int ang = retVal;
  return ang;
}

void printTime(int time_for_motor[]){
  Serial.print(time_for_motor[0], DEC);
  Serial.print(':');
  Serial.print(time_for_motor[1], DEC);
  Serial.print(':');
  Serial.print(time_for_motor[2], DEC);
  Serial.print("\n");
}

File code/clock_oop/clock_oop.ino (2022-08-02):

#define FASTLED_INTERNAL
#define NUM_LEDS 3
#define LED_TYPE WS2812
#define COLOR_ORDER GRB
#define TCAADDR 0x70
#define ENCADDR 0x36
#include <Wire.h>
#include<DS3231.h>
#include <TimerOne.h>
#include <AS5600.h>
#include <FastLED.h>
// RGB LEDs
CRGB leds[NUM_LEDS];
const int LED_DATA = 7;

// Buzzer
const int Buzzer = 8;

// Motor index
enum Index {H_L, H_R, M_L, M_R, S_L, S_R};
const int motor_num = 6;
const int Motor_pin[motor_num] = {9, 2, 3, 4, 5, 6};

//state machine
class StateMachine{
private:
    bool State[motor_num];
public:

};
/*******************************
 * Motor: closed control useing AS5600
 * Control by position loop
 * *****************************/
// Periods caculation:
//1.8 degrees per step (ms = 1/8) 
// One number lasts for 36 degree, namely 20 * 8 = 160 steps
// For SR, we want it to rotate constantly, period = 6250 us
// For SL, we want it to just rotate at the 9th second, and finish rotating in one second, period = 6250
// For ML and MR, we want it to rotate at the 8th second, and finish rotating in two seconds, period = 2 * base 
// For HL and HR, we want it to rotate at the 5th second, and finish rotating in five seconds, period = 5 * base  
class PWM{
private:
    const static int gear_ratio = 25; // ratio of gear and motor
    const static int base_period = 6250; //period of SR
    unsigned long period; 
    bool level = 0;
public:
    PWM() = delete;
    PWM(Index index);
    ~PWM() = default;
    unsigned long get_period(){return period;}
    bool get_level(){return level;}
    void flip(){level = !level;}
};
PWM::PWM(Index index){
    switch (index)
    {
        case S_R:
        case S_L:
            period = base_period / gear_ratio;     
            break;
        case M_L: 
        case M_R:
            period = 2 * base_period / gear_ratio;
            break;
        case H_L:
        case H_R:
            period = 5 * base_period / gear_ratio;
            break;
        default:
            break;
    }
}

class Motor{
private:
    Index index;
    bool ENA;
    int angle;
    AS5600 Encoder;
public:
    PWM pwm;
    const int pin;
    Motor() = default;
    Motor(Index _index):index(_index), pin(Motor_pin[_index]), ENA(false),pwm(_index){};
    ~Motor() = default;
    void Init();
    void tcaselect();
    void enable(){ENA = true;}
    void disable(){ENA = false;}
    bool ifEnabled(){return ENA;}
    const static int dirPin = 10;
};

void Motor::tcaselect(){
    int i = index;
    if(i > motor_num) return;
    Wire.beginTransmission(TCAADDR);
    Wire.write(1 << i);
    Wire.endTransmission();
}

void Motor::Init(){
    pinMode(pin, OUTPUT);
    digitalWrite(dirPin, LOW);

    tcaselect();
    Serial.print("TCA Port #"); Serial.println(index);
    Wire.beginTransmission(ENCADDR);
    if (!Wire.endTransmission()) {
        Serial.print("Found Encoder "); Serial.println(index);
    }
    else{
        Serial.println("Motor "); Serial.print(index); Serial.println("'s Encoder not found");
    }
}

Motor Motors[] = {Motor(H_L), Motor(H_R),Motor(M_L),Motor(M_R),Motor(S_L),Motor(S_R)};

/*****************************************
 * Time displayed by the motor  
 * getTime from DS3231  
 * ****************************************/
// Clock DS3231
DS3231 ds3231;
bool h12 = false; // don't use 12 hours mode
bool apm; // useless under non 12 hours mode

class Motor_Time{
private:
   // Number for each motor
   int time_number[motor_num]; 
   // Time to control the rotation of the motor
   unsigned long time_micros[motor_num];
public:
    Motor_Time() = default;
    ~Motor_Time() = default;
    void Init();
    void getTime();
    void printTime();
    void ChangeState(Motor Motors[]);
    void setup_motor(Motor Motors[]);
};

void Motor_Time::Init(){
    byte index = 0;
    char endMarker = '\n';
    char rc;
    char Serial_Res[motor_num];
    Serial.print("Set the time(Format:xxxxxx\\n):\n");
  
    while (true) {
      while (Serial.available() == 0);
      rc = Serial.read();
      if (rc != endMarker)
        Serial_Res[index++] = rc;
      else
        break;
    }
    for (int i = 0; i < motor_num; i++)
        time_number[i] = (Serial_Res[i] - '0') ; 
    
    ds3231.setSecond((time_number[0] - '0') * 10 + (time_number[1] - '0'));//Set the second
    ds3231.setMinute((time_number[2] - '0') * 10 + (time_number[3] - '0'));//Set the minute
    ds3231.setHour((time_number[4] - '0') * 10 + (time_number[5] - '0'));  //Set the hour
    Serial.print("Time Set:");
    printTime();
    for (int i = 0; i < motor_num; i++)
        time_micros[i] = micros();
}

void Motor_Time::getTime(){
    int ds3231_time[3];
    ds3231_time[0] = ds3231.getHour(h12, apm);
    ds3231_time[1] = ds3231.getMinute();
    ds3231_time[2] = ds3231.getSecond();
    for (int i = 0; i < motor_num; i++)
        if(i % 2) time_number[i] = ds3231_time[i / 2] % 10;
        else time_number[i] = ds3231_time[i / 2] / 10;
}

void Motor_Time::printTime(){
    Serial.print(time_number[0], DEC);
    Serial.print(time_number[1], DEC);
    Serial.print(':');
    Serial.print(time_number[2], DEC);
    Serial.print(time_number[3], DEC);
    Serial.print(':');
    Serial.print(time_number[4], DEC);
    Serial.print(time_number[5], DEC);
    Serial.print("\n");
}

void Motor_Time::ChangeState(Motor Motors[]){
    (time_number[S_R] == 9) ? Motors[S_L].enable() : Motors[S_L].disable(); 
    if((time_number[S_L] == 5) && (time_number[S_L] == 8)){
       Motors[M_R].enable();
       if(time_number[M_R] == 9) Motors[M_L].enable(); 
       else Motors[M_L].disable();
    }
    else Motors[M_R].disable();
    if((time_number[M_L] == 5) && (time_number[M_R] == 9) && (time_number[S_L] == 5) && (time_number[S_L] == 5)){
        Motors[H_R].enable();
        if(time_number[H_R] == 9) Motors[H_L].enable();
        else Motors[H_L].disable();
    }
    else Motors[H_R].disable();
}

void Motor_Time::setup_motor(Motor Motors[]){
    ChangeState(Motors);
    for (int i = 0; i < motor_num; i++)
    {
        if(Motors[i].ifEnabled())
            if(micros() - time_micros[i] > (Motors[i].pwm.get_period() / 2)){
                Motors[i].pwm.flip();
                digitalWrite(Motors[i].pin, Motors[i].pwm.get_level());
                time_micros[i] = micros();
            }
    }
}

Motor_Time motor_time;

void setup() {
    Wire.begin();
    Serial.begin(115200);
    for (int i = 0; i < motor_num; i++)
      Motors[i].Init();
    //LEDS.addLeds<LED_TYPE, LED_DATA, COLOR_ORDER>(leds, NUM_LEDS);
    //FastLED.setBrightness(255);
    while (Serial.available() > 0) {
      Serial.flush();
    }
    motor_time.Init();
    Timer1.initialize(Motors[S_R].pwm.get_period() / 2); //Initialize timer with half period of SR
    Timer1.attachInterrupt(PWM_SR);  
}

void loop() {
    motor_time.getTime();
    //motor_time.printTime();
    motor_time.setup_motor(Motors);
   
//  Readangle(angle);
}
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

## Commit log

2022-07-28 Bug fix
    [DC-DC.sch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]
2022-07-28 Change the inductor
    [DC-DC.kicad_sch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]
